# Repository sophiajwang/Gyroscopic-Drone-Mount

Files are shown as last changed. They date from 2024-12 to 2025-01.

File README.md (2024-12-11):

# Gyroscopic Test Rig
#### Sophia Wang and Tshering Dorji

<p align="center">
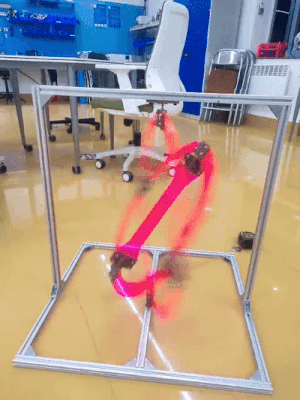
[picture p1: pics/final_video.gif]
animated
  
  <br  /> 3-axis (yaw/pitch/roll) for tuning flight controller pre-launch.
</p>

## Assembly
<p align="center">
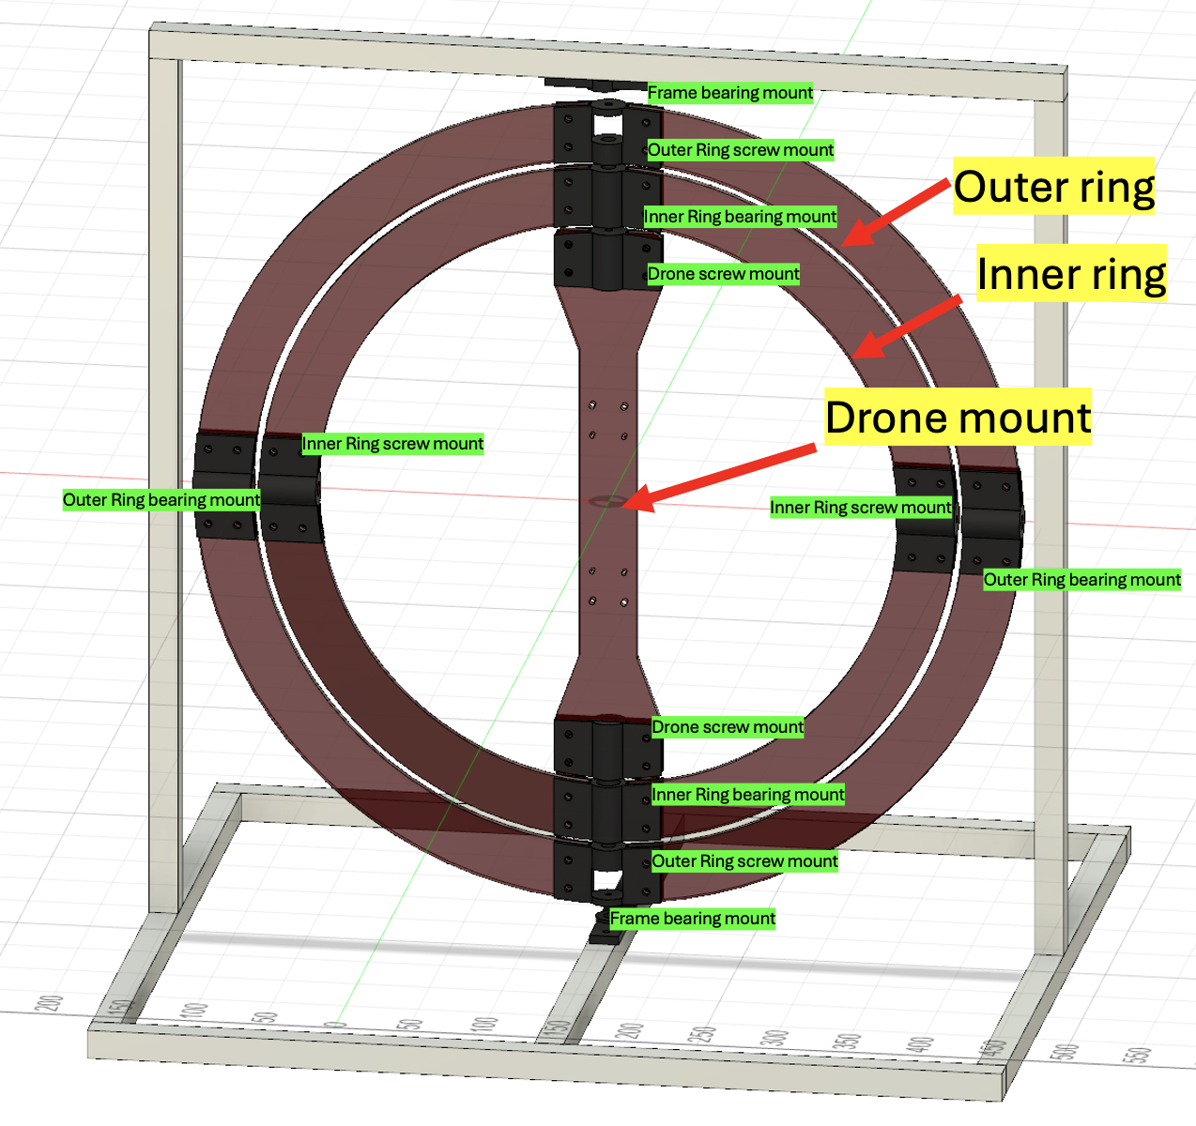
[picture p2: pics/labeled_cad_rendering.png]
  
  <br  /> Assembly Diagram
</p>

## Parts 
### Tools
| Name | Purpose |
| --- | --- |
| Circular saw machine | aluminum extrusions|
| Sanding machine/sandpaper| aluminum extrusions |
| M4 and M5 allen keys | assembly|
| Wrench or needle nose plier | assembly|

### Frame
| Section | Part | Details | Quantity |
| --- | --- | --- | --- |
| Base | Aluminum Extrusion [^1] | 52.5 cm | 3 |
| Base | Aluminum Extrusion | 63 cm | 2 |
| Base | 2020 Corner Bracket | 30 mm x 30 mm | 8 |
| Base | M5x10, knurled cylinder head| | 16 |
| Base | M5 T-nut| | 16 |
| Column | Aluminum Extrusion | 60.5 cm| 2 |
| Column | 2020 Corner Bracket | 30 mm x 30 mm | 4 |
| Column | M5x10, knurled cylinder head| | 8 |
| Column | M5 T-nut| | 8 |
| Top beam | Aluminum Extrusion | 63 cm | 1 |
| Top beam | 2020 Corner Bracket | 30 mm x 30 mm | 2 |
| Top beam | M5x10, knurled cylinder head| | 4 |
| Top beam | M5 T-nut| | 4 |

[^1]: aluminum extrusions are 20 mm x 20 mm, T-Slot 80/20

### Rig
| Section | Part | Details | Quantity |
| --- | --- | --- | --- |
| Mount | Drone Mount | Laser Cut [^2] | 1 |
| Mount | Drone screw mount | 3D print [^3] | 1 |
| Mount | M5x15, knurled cylinder head |  | 8 |
| Mount | M5 nut [^4] |  | 8 |
| Inner Ring | Inner Ring | Laser Cut | 4 |
| Inner Ring | Inner ring screw mount | 3D print | 2 |
| Inner Ring | Inner ring bearing mount | 3D print | 2 |
| Inner Ring | M5x15, knurled cylinder head | ring interconnects | 16 |
| Inner Ring | M5 nut | ring interconnects | 16 |
| Inner Ring | M5x25, knurled cylinder head | bearing shaft [^5] | 2 |
| Inner Ring | M5 nut | bearing shaft | 4 |
| Inner Ring | Bearing (5x16x5mm)	 | | 2 |
| Outer Ring | Outer Ring | Laser Cut | 4 |
| Outer Ring | Outer ring screw mount | 3D print | 2 |
| Outer Ring | Outer ring bearing mount | 3D print | 2 |
| Outer Ring | M5x15, knurled cylinder head | ring interconnects | 16 |
| Outer Ring | M5 nut | ring interconnects | 16 |
| Outer Ring | M5x25, knurled cylinder head | bearing shaft | 2 |
| Outer Ring | M5 nut | bearing shaft | 4 |
| Outer Ring | Bearing (5x13x4mm) | | 2 |
| Frame | Frame Bearing Mount [^6] | 3D print | 2 |
| Frame | M4x30, button cap screw | bearing shaft | 2 |
| Frame | M4 nut | bearing shaft | 6 |

[^2]: 5.5 mm acrylic
[^3]: 30% infil
[^4]: If nuts are difficult to find, you can thread a self-tightening nut with significant elbow grease.
[^5]: We're working around the supply here. Better practice would be to use a fitted 5 mm shaft. Here, we're placing a loosely fitting 5 mm bolt through the shaft of the bearing, and securing with one nut at either end.
[^6]: Again, working around supply. Best case would have been to find some M5x30 bolts, but we were only able to find M4 ones of sufficient length. Here, we're securing the bearing against the head of the bolt and the exacting pressure of the aluminum columns (better to add another nut to relieve precision of extrusions), then securing the screw mount with two nuts.

## Our Process

<p align="middle">
  <br  /> 
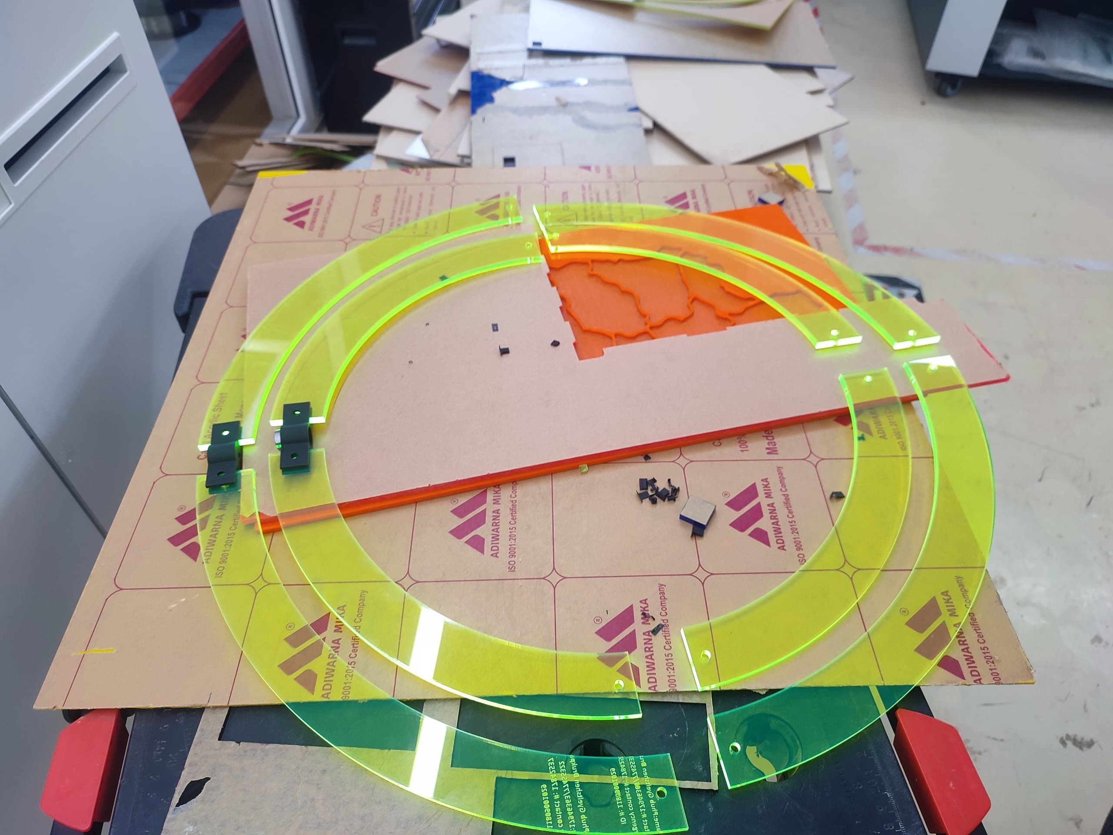
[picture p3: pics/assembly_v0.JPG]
  
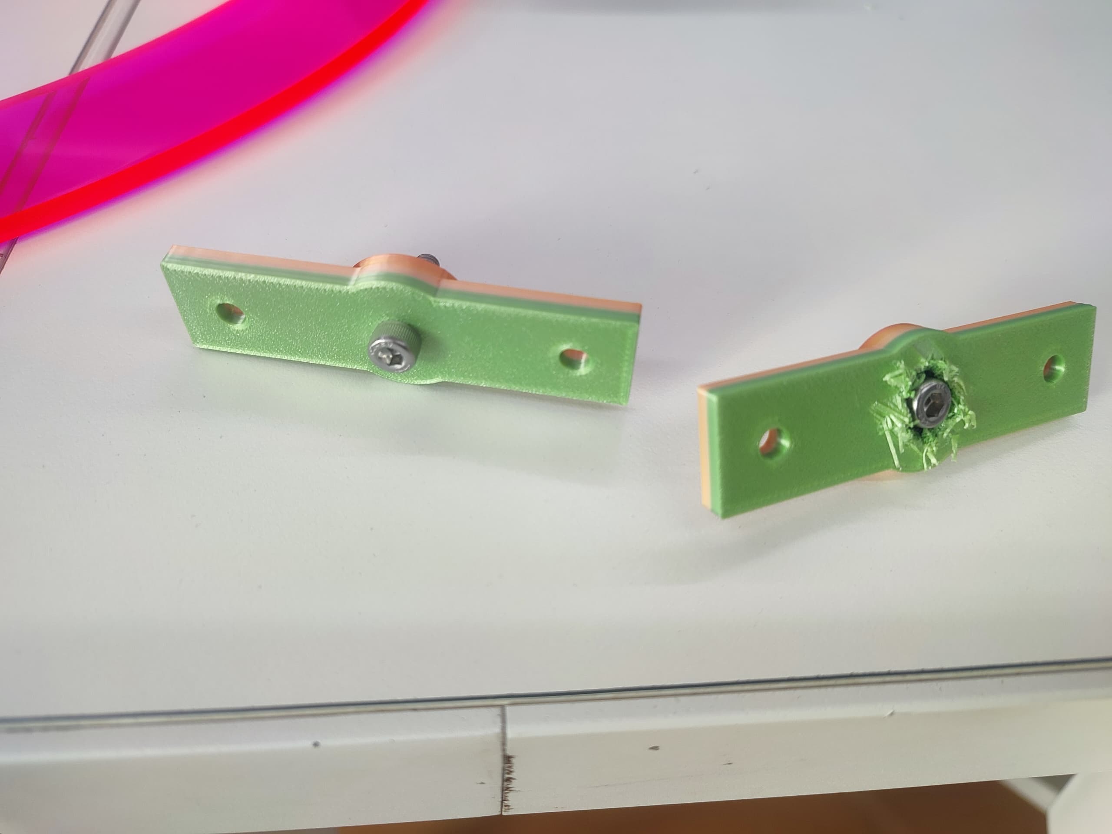
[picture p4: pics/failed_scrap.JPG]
   
  <br  /> attempt 1
</p>

There was lots of trial and error. Our first attempt at nesting the rings was a miscalculation of the degrees of freedom from only one fastener on each side of the screw/bearing mount. These prints don't do well with threading. The shredded PLA you see below is the result of no-tolerance prints, which we quickly adjusted to + 0.15 mm to adjust for post plastic shrinkage. 

<p align="middle">
  <br  /> 
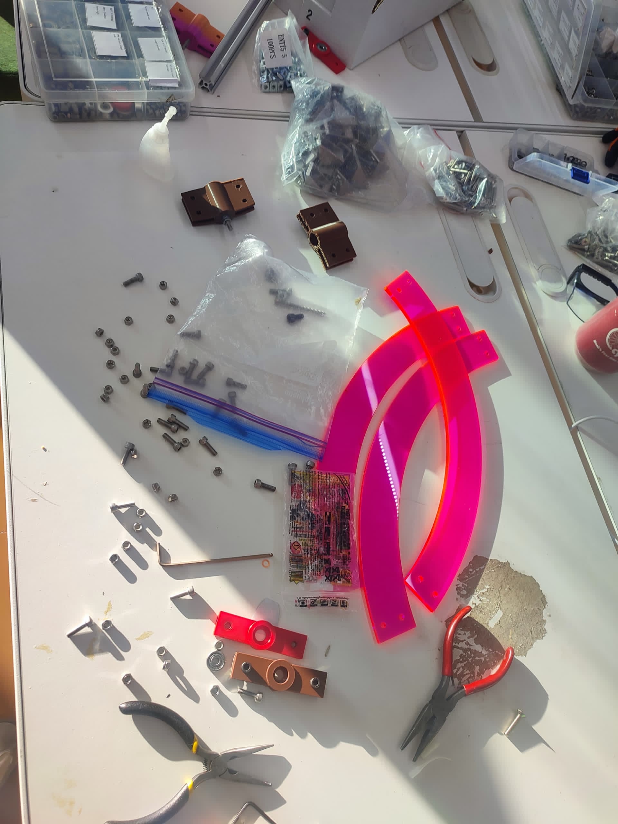
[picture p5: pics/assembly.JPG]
  
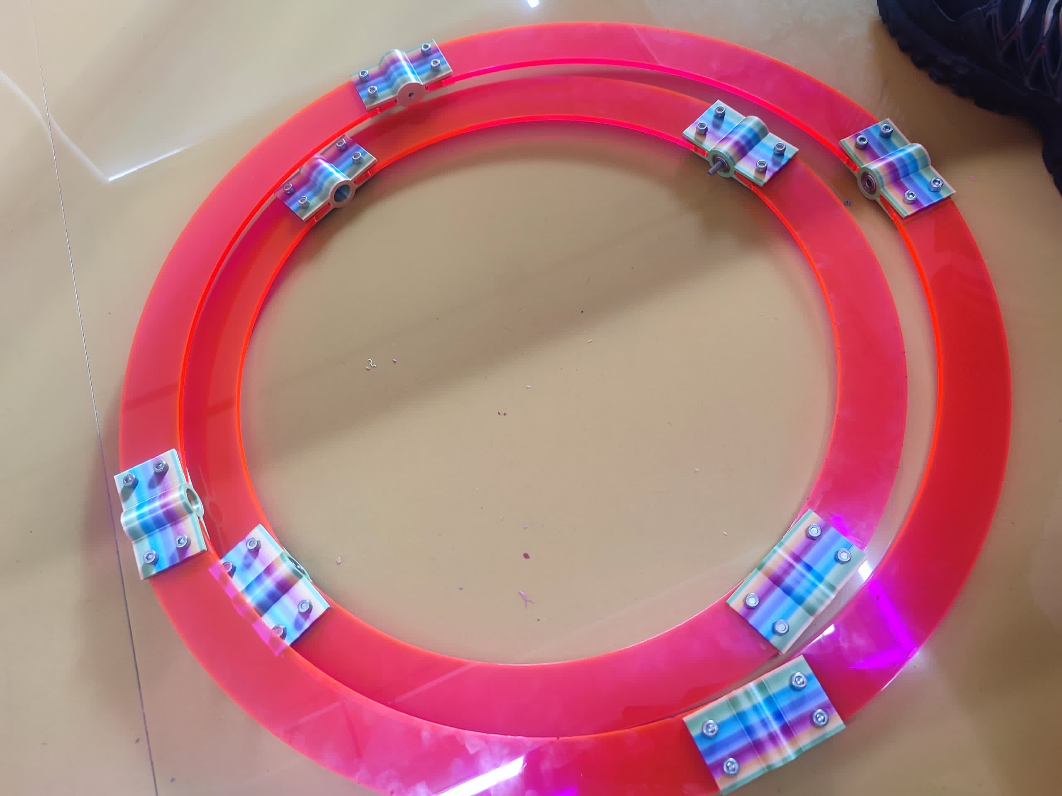
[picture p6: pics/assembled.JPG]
   
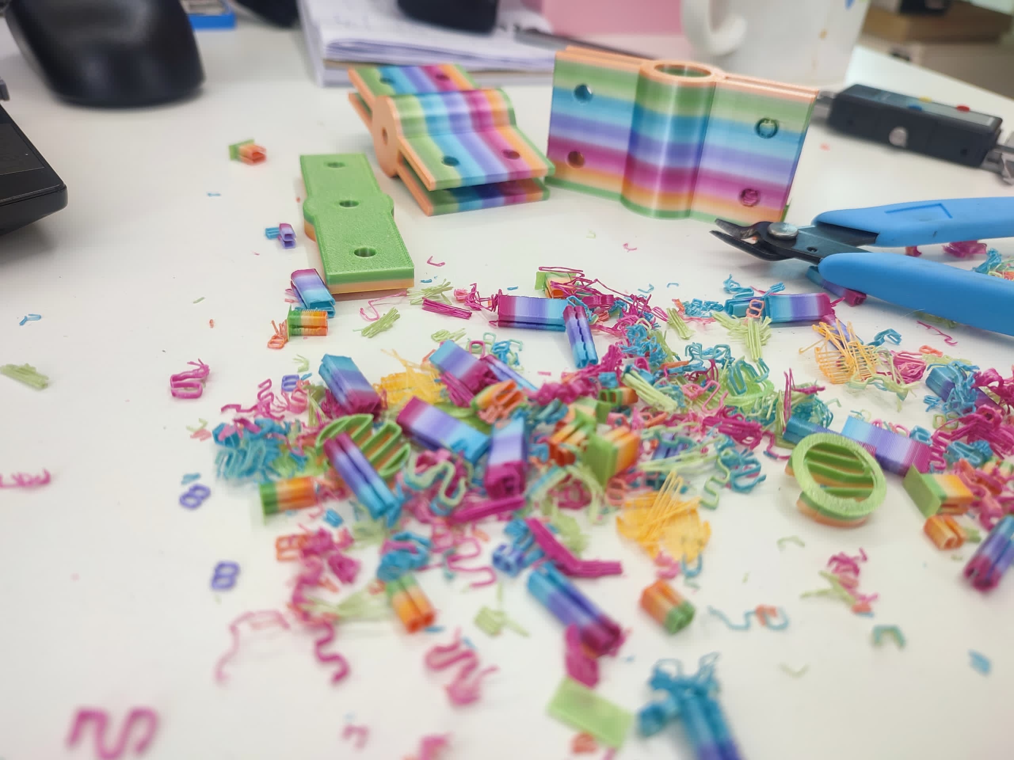
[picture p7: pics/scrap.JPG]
   
  <br  /> attempt 2
</p>

On attempt 2, the realization set in that the M5 screw was too loose as a shaft for the bearing, and without a tight fitting shaft in supply, we opted for a handy nut to secure the bearing's rotational axis. You can see the shredded PLA as we tested this theory out on our existing bearing mounts and realized we needed to redesign to compensate for the extra nut. 

<p align="middle">
  <br  /> 
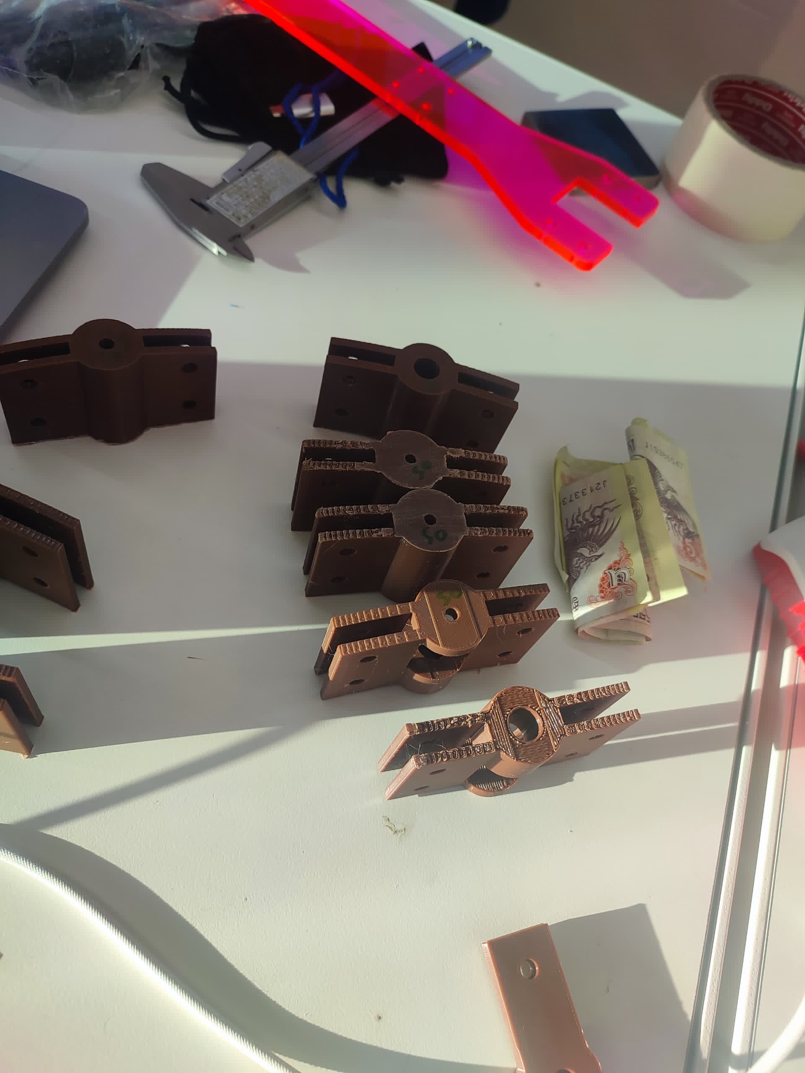
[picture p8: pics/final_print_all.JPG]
  
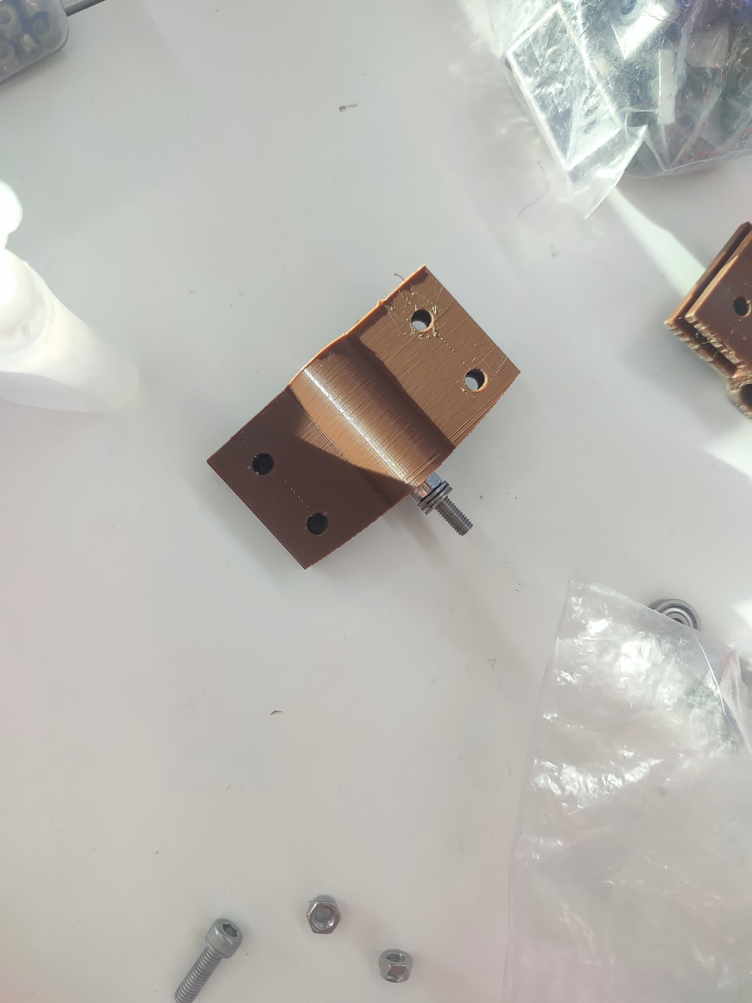
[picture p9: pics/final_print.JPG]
   
  <br  /> attempt 3
</p>

Finally, we could begin cutting the extrusions for the frame and assemble!

<p align="middle">
  <br  /> 
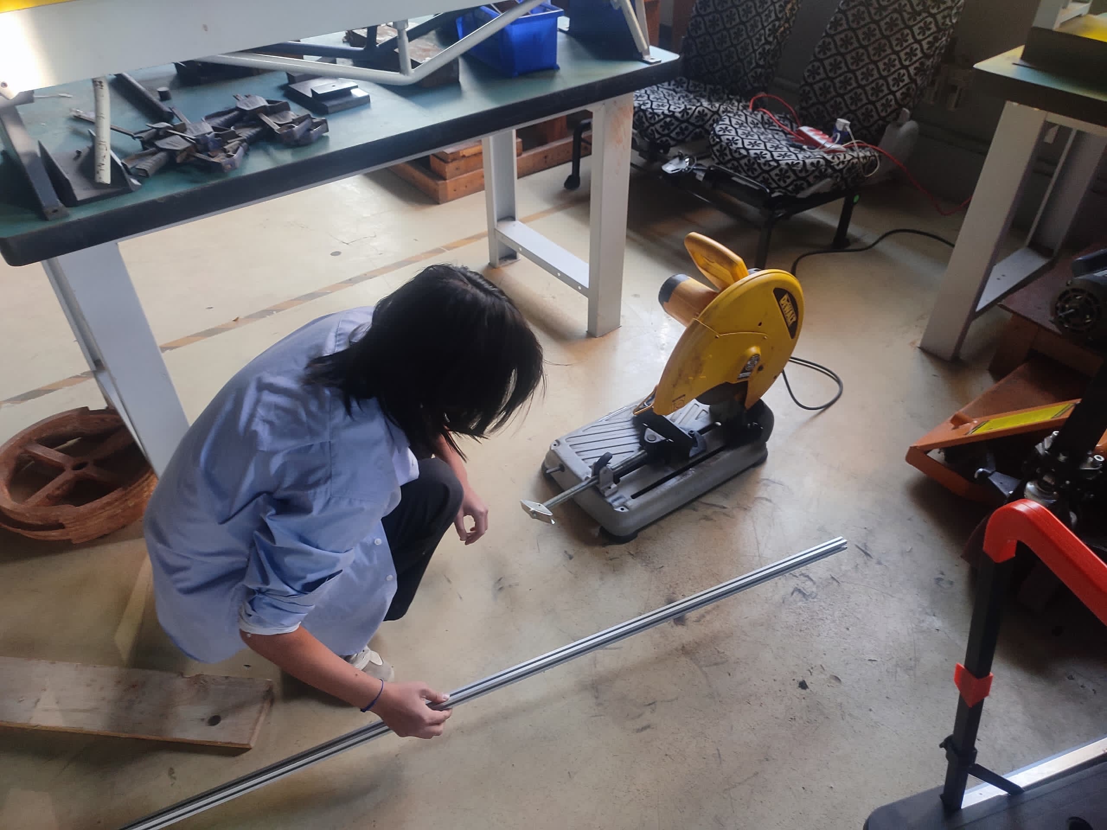
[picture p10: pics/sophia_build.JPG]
  
   
  <br  /> circular saw
</p>

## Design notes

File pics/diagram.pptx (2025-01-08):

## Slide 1

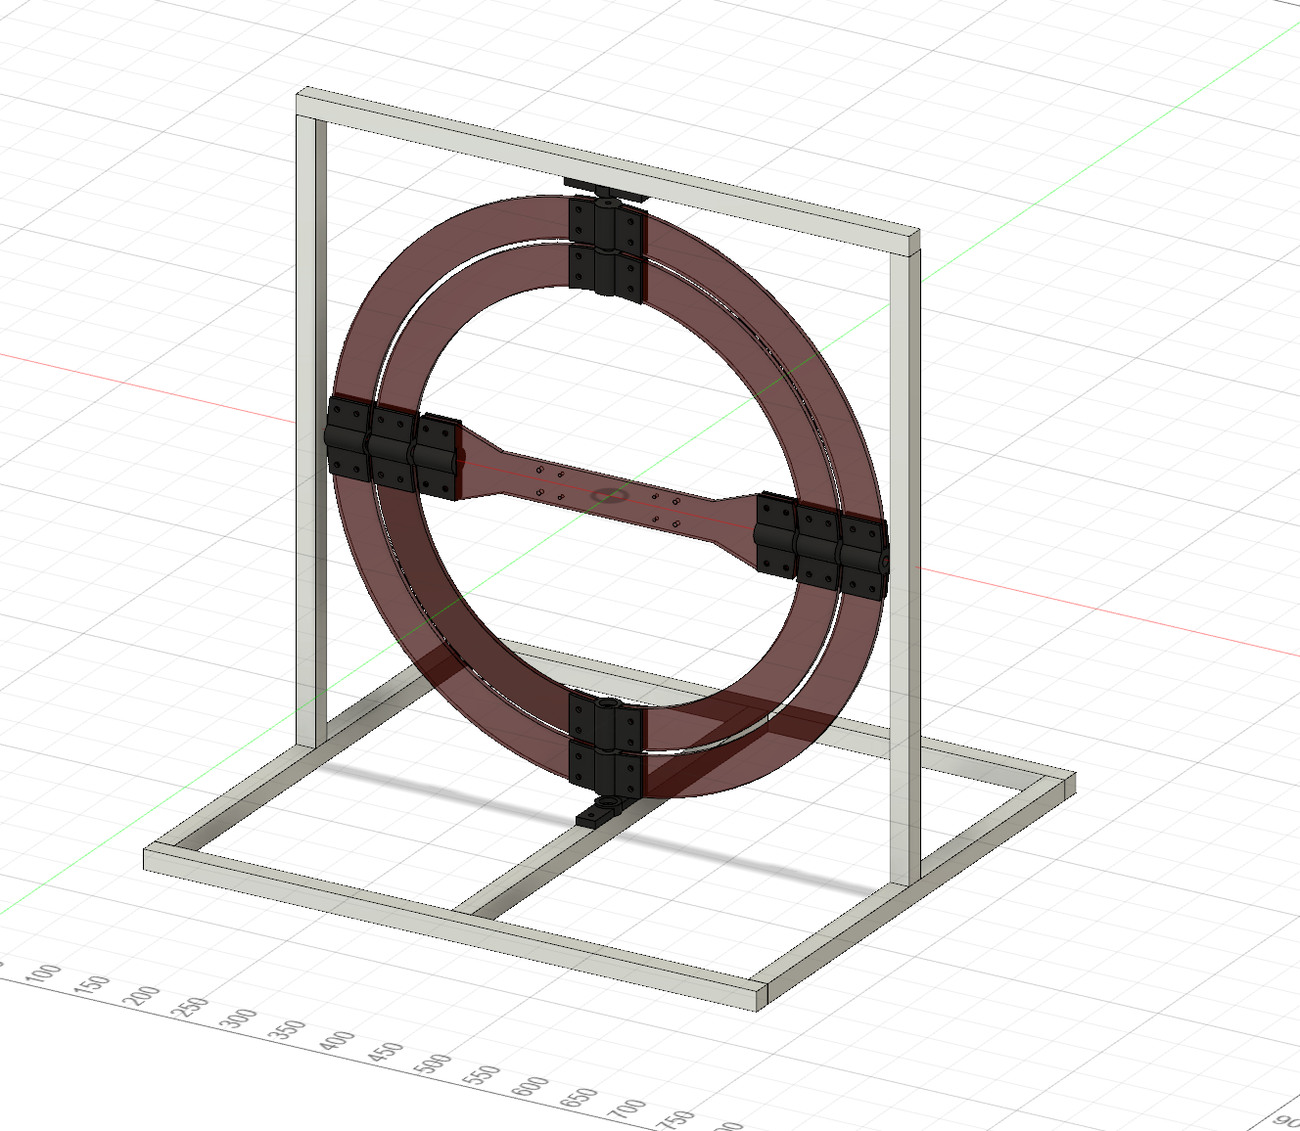
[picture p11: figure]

Frame bearing mount

Outer Ring screw mount

Outer ring

Inner Ring screw mount

Inner ring

Outer Ring bearing mount

Inner Ring bearing mount

Drone mount

Drone screw mount

Drone screw mount

Inner Ring bearing mount

Outer Ring bearing mount

Inner Ring screw mount

Frame bearing mount

Outer Ring screw mount

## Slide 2

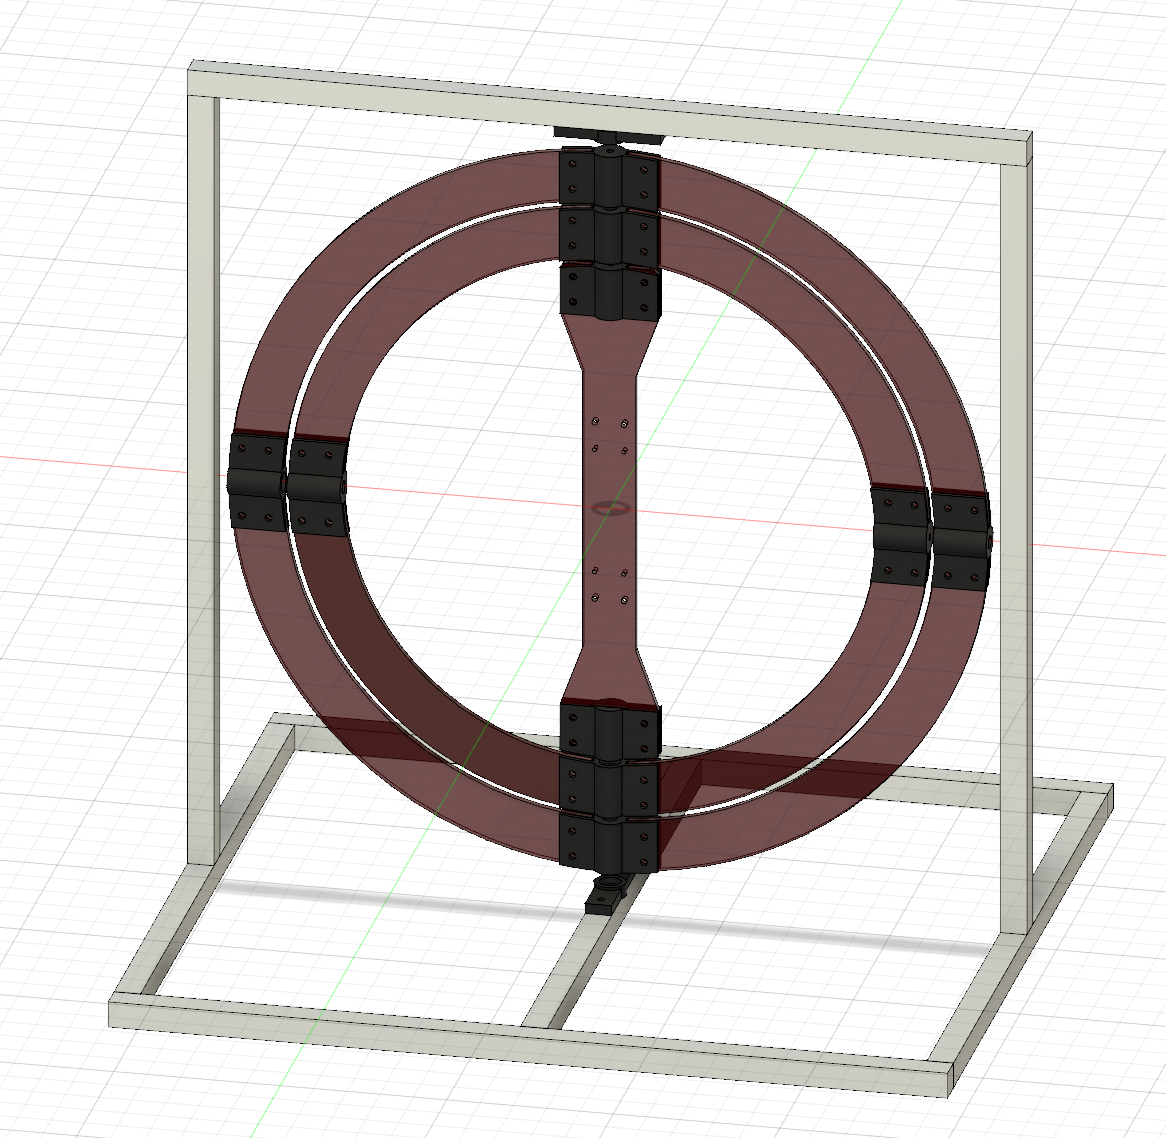
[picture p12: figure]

Frame bearing mount

Outer Ring screw mount

Inner Ring bearing mount

Outer ring

Inner ring

Drone screw mount

Inner Ring screw mount

Drone mount

Inner Ring screw mount

Outer Ring bearing mount

Outer Ring bearing mount

Drone screw mount

Inner Ring bearing mount

Outer Ring screw mount

Frame bearing mount

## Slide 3

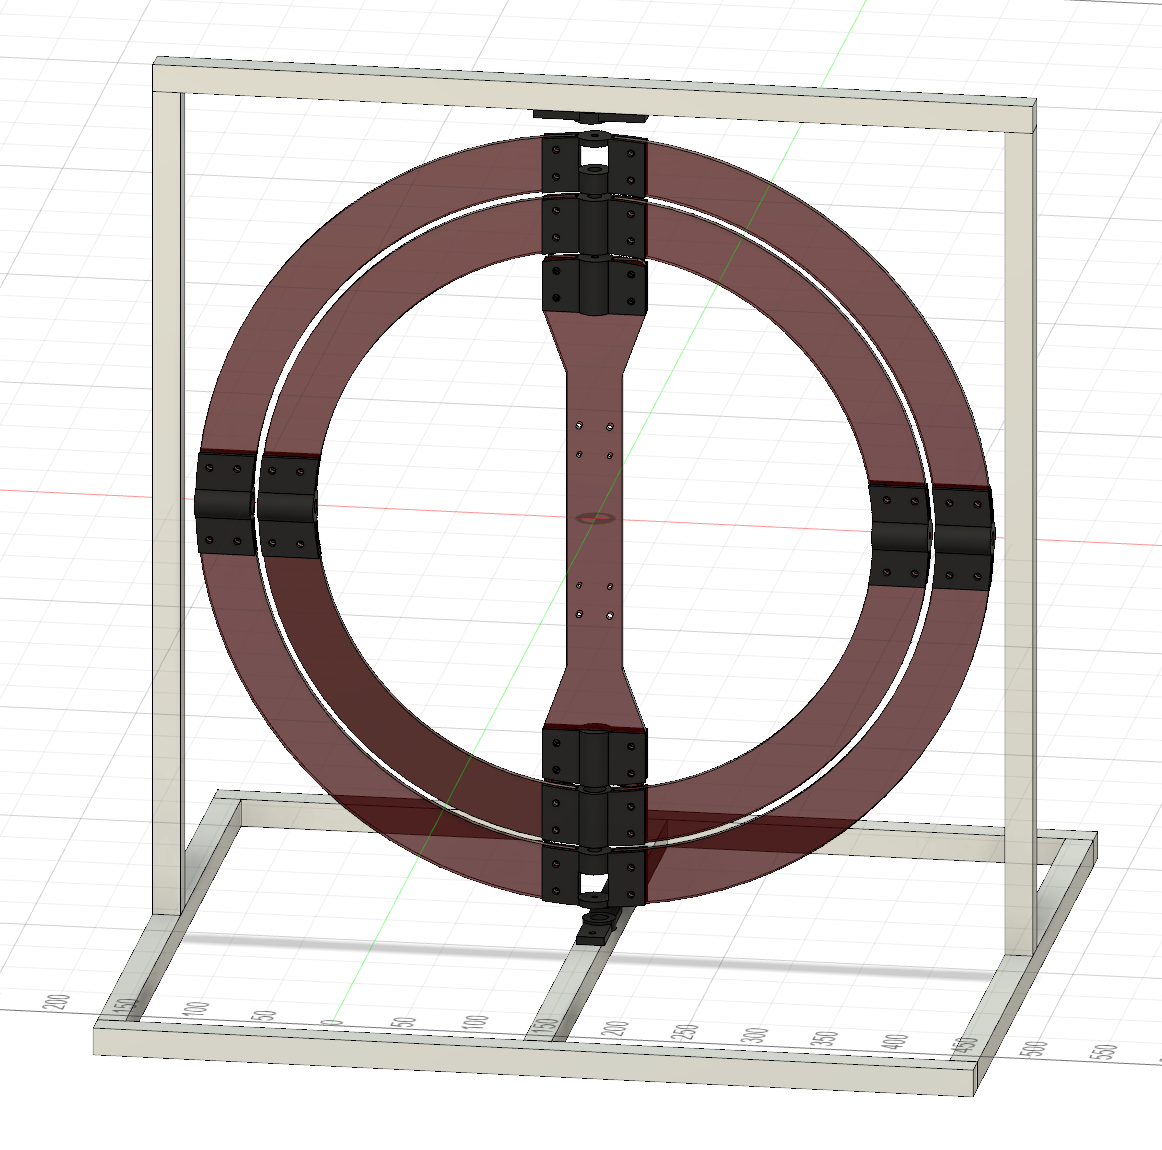
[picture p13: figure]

Frame bearing mount

Outer Ring screw mount

Inner Ring bearing mount

Outer ring

Inner ring

Drone screw mount

Inner Ring screw mount

Drone mount

Inner Ring screw mount

Outer Ring bearing mount

Outer Ring bearing mount

Drone screw mount

Inner Ring bearing mount

Outer Ring screw mount

Frame bearing mount

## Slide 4

Outer ring

Inner ring

Drone mount

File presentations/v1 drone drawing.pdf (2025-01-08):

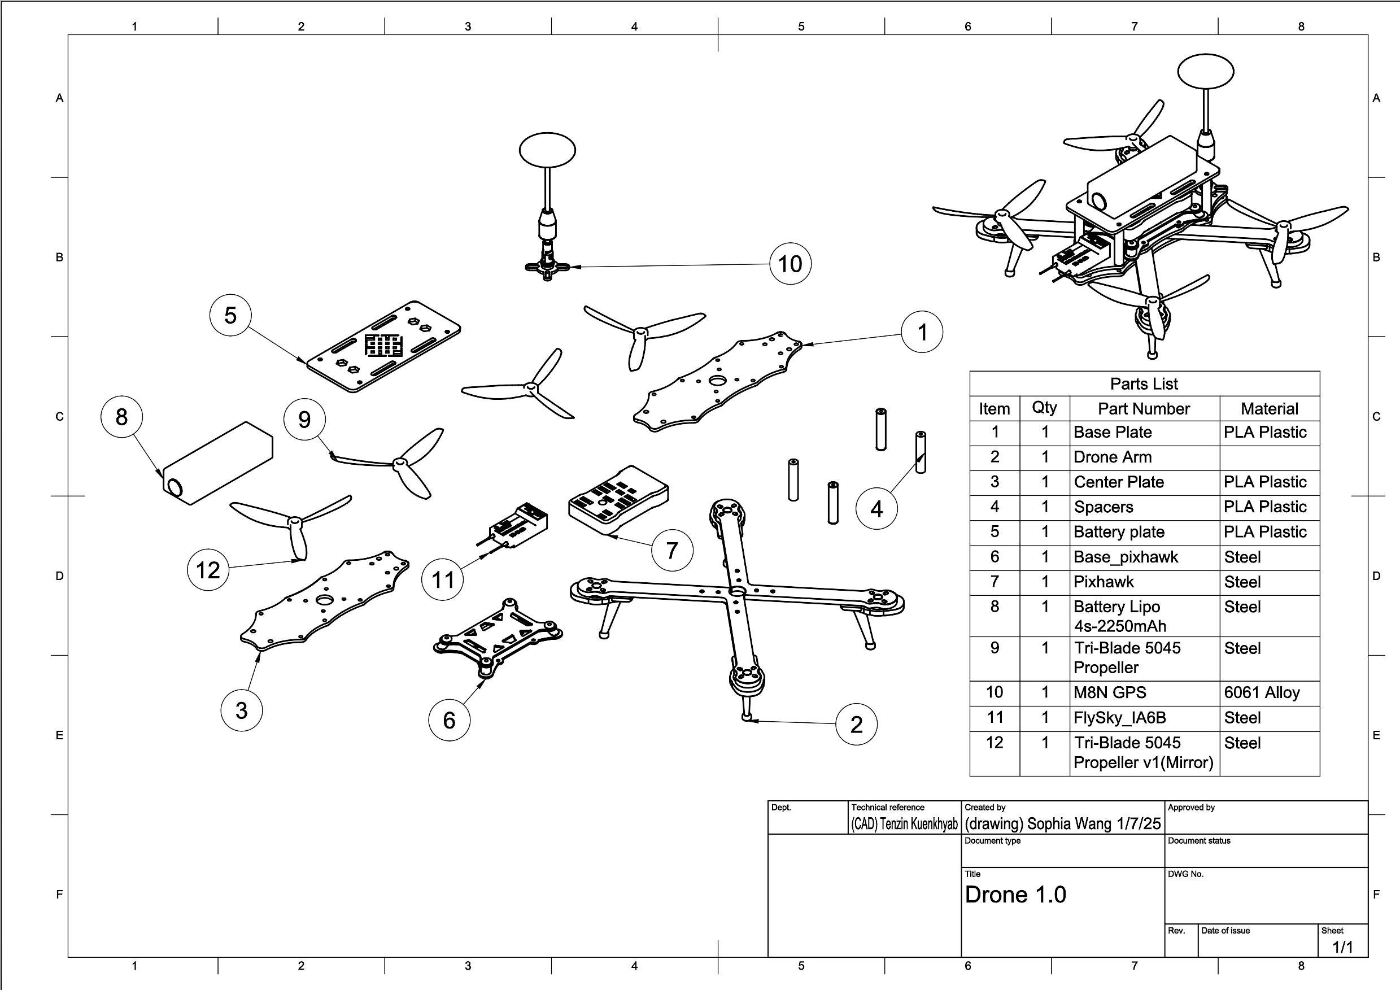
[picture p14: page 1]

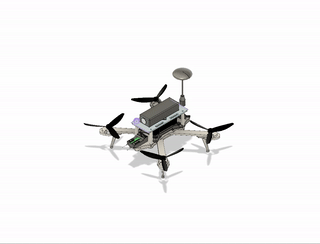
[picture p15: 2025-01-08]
presentations/drone_explode_view.gif

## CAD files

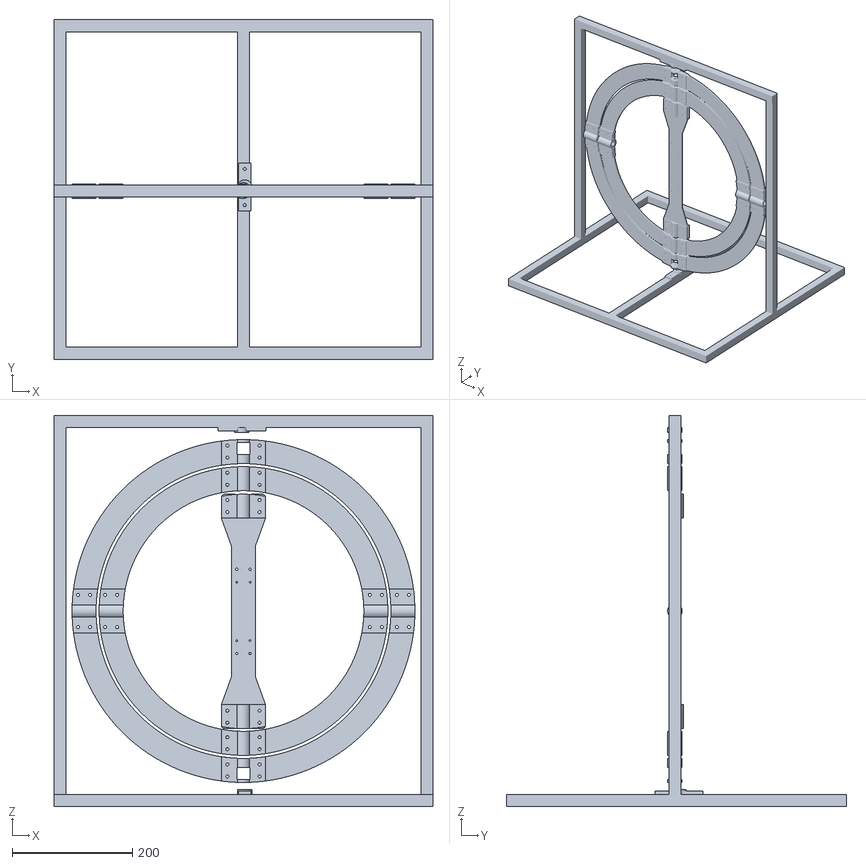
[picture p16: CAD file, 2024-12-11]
cad/Quadcopter Testbed Assembly.stl
630.2 x 564.5 x 650.5

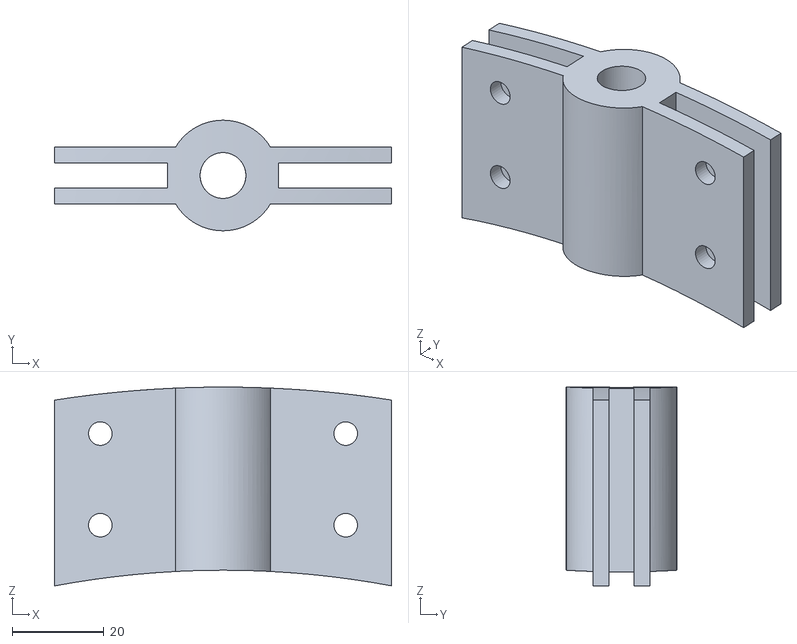
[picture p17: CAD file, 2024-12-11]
cad/inner ring bearing mount.stl
73.6 x 24.1 x 43.4

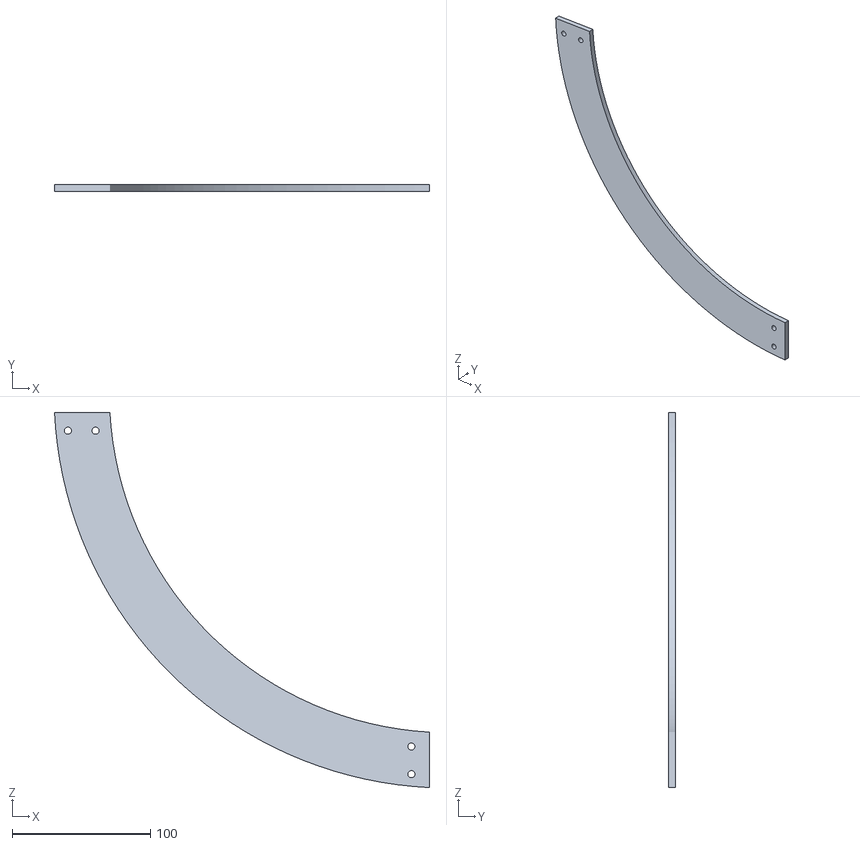
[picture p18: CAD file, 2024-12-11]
cad/outer ring.stl
271.0 x 5.00 x 271.1

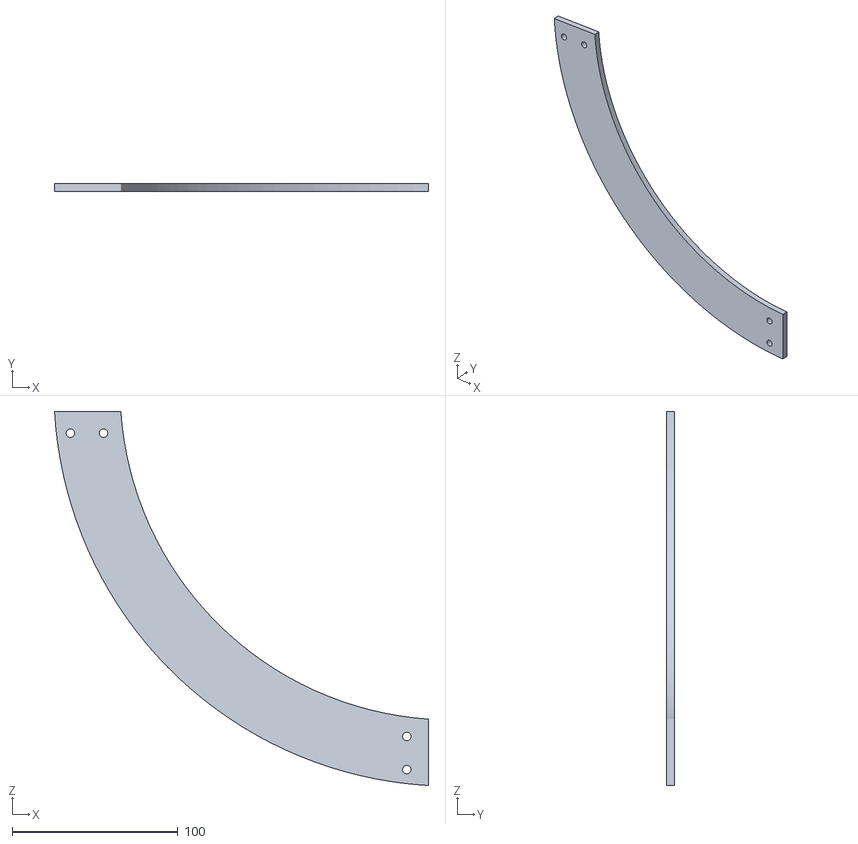
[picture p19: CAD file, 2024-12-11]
cad/inner ring.stl
225.9 x 5.00 x 225.9

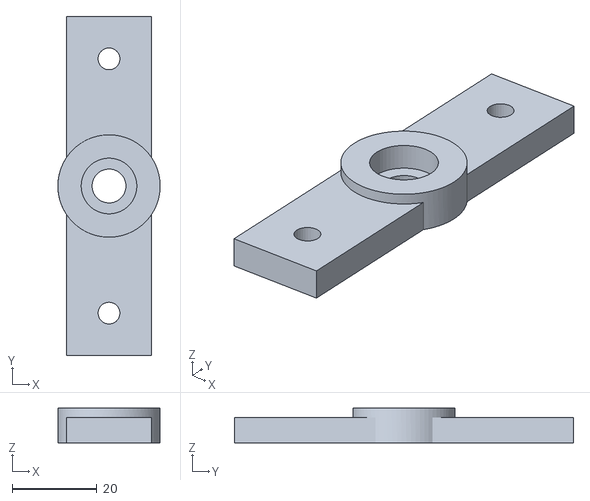
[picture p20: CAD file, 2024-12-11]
cad/frame bearing mount.stl
24.1 x 80.0 x 8.15

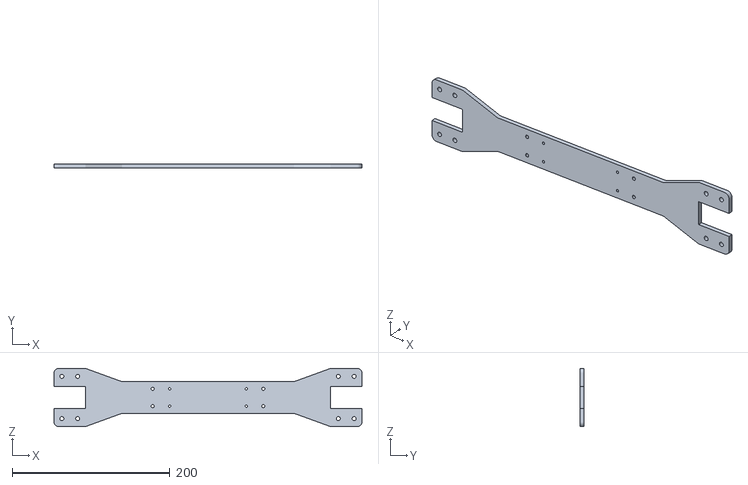
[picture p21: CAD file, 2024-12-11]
cad/drone mount.stl
390.0 x 5.00 x 73.6

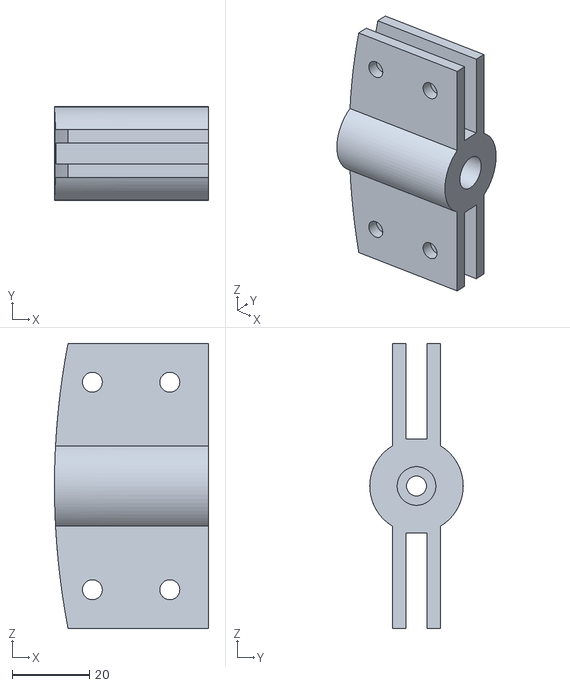
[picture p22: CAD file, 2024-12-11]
cad/drone screw mount.stl
39.8 x 24.2 x 73.6

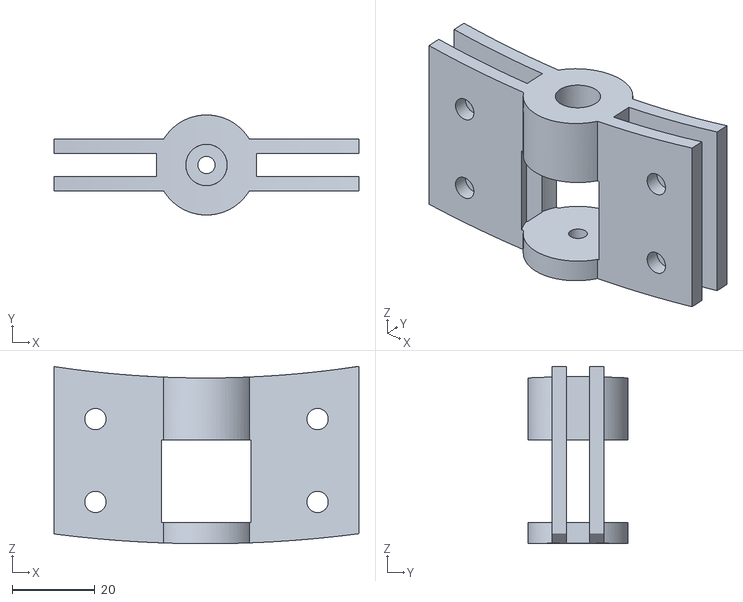
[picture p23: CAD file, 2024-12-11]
cad/outer ring screw mount.stl
73.6 x 24.2 x 42.8

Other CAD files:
cad/outer ring bearing mount.stl
cad/inner ring screw mount.stl
cad/Quadcopter Testbed Assembly.f3d

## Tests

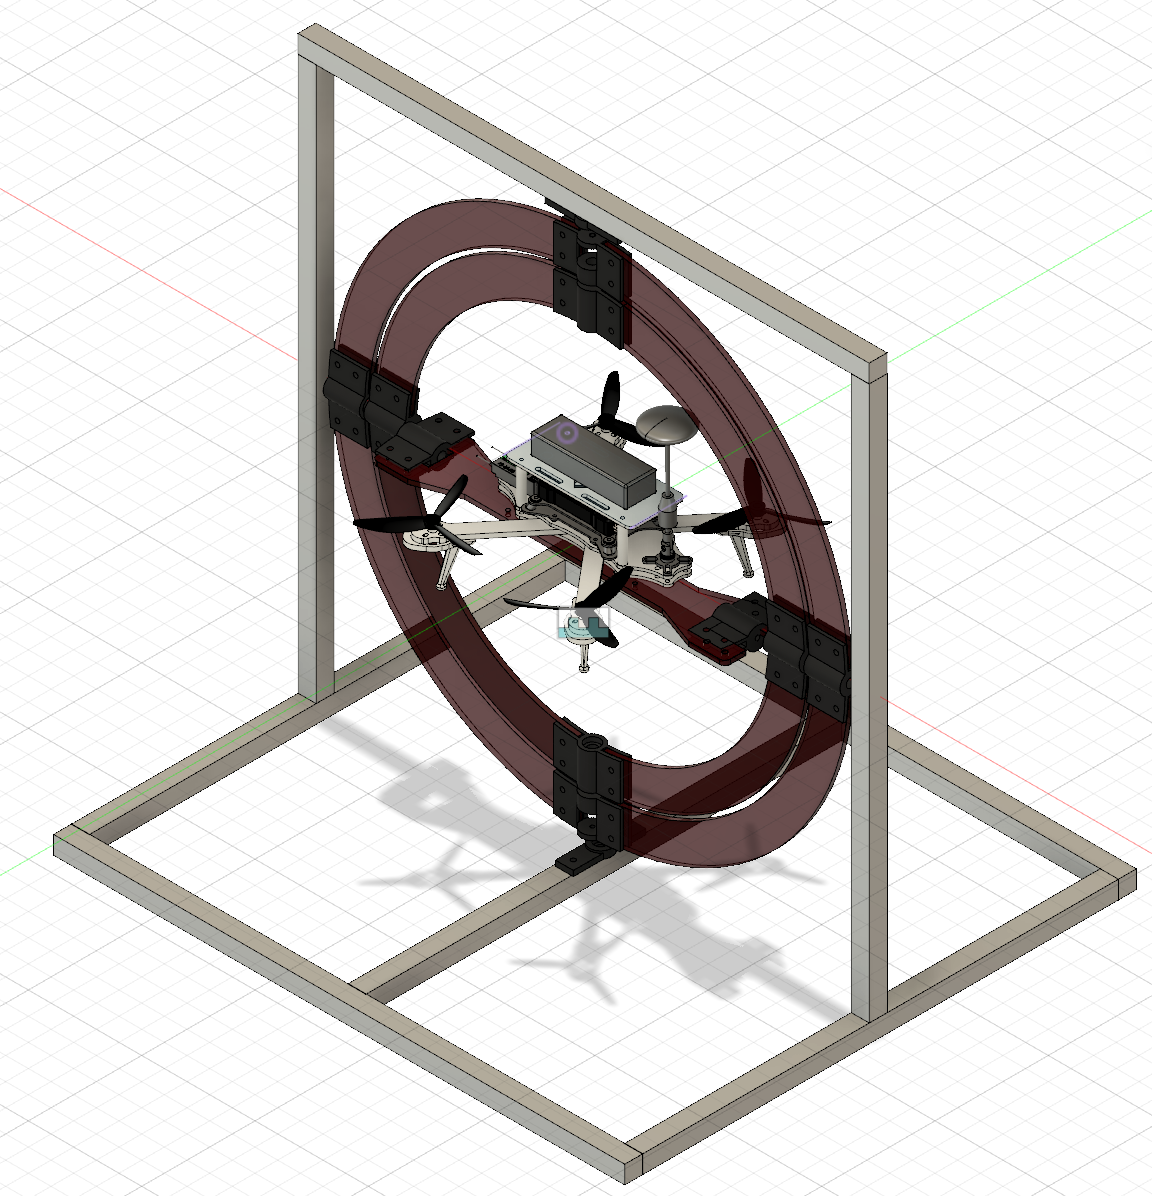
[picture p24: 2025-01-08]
presentations/cad_drone_testrig.png

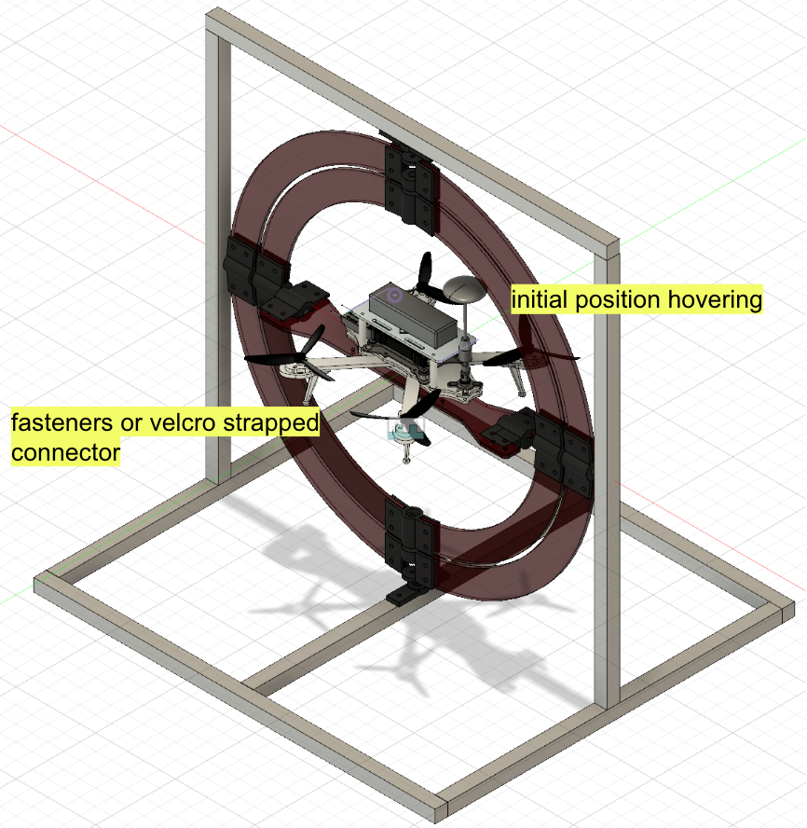
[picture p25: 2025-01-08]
presentations/labeled_cad_drone_testrig.png

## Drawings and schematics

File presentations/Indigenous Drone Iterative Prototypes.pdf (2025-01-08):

# v3 Test Rig

# v3 Controller

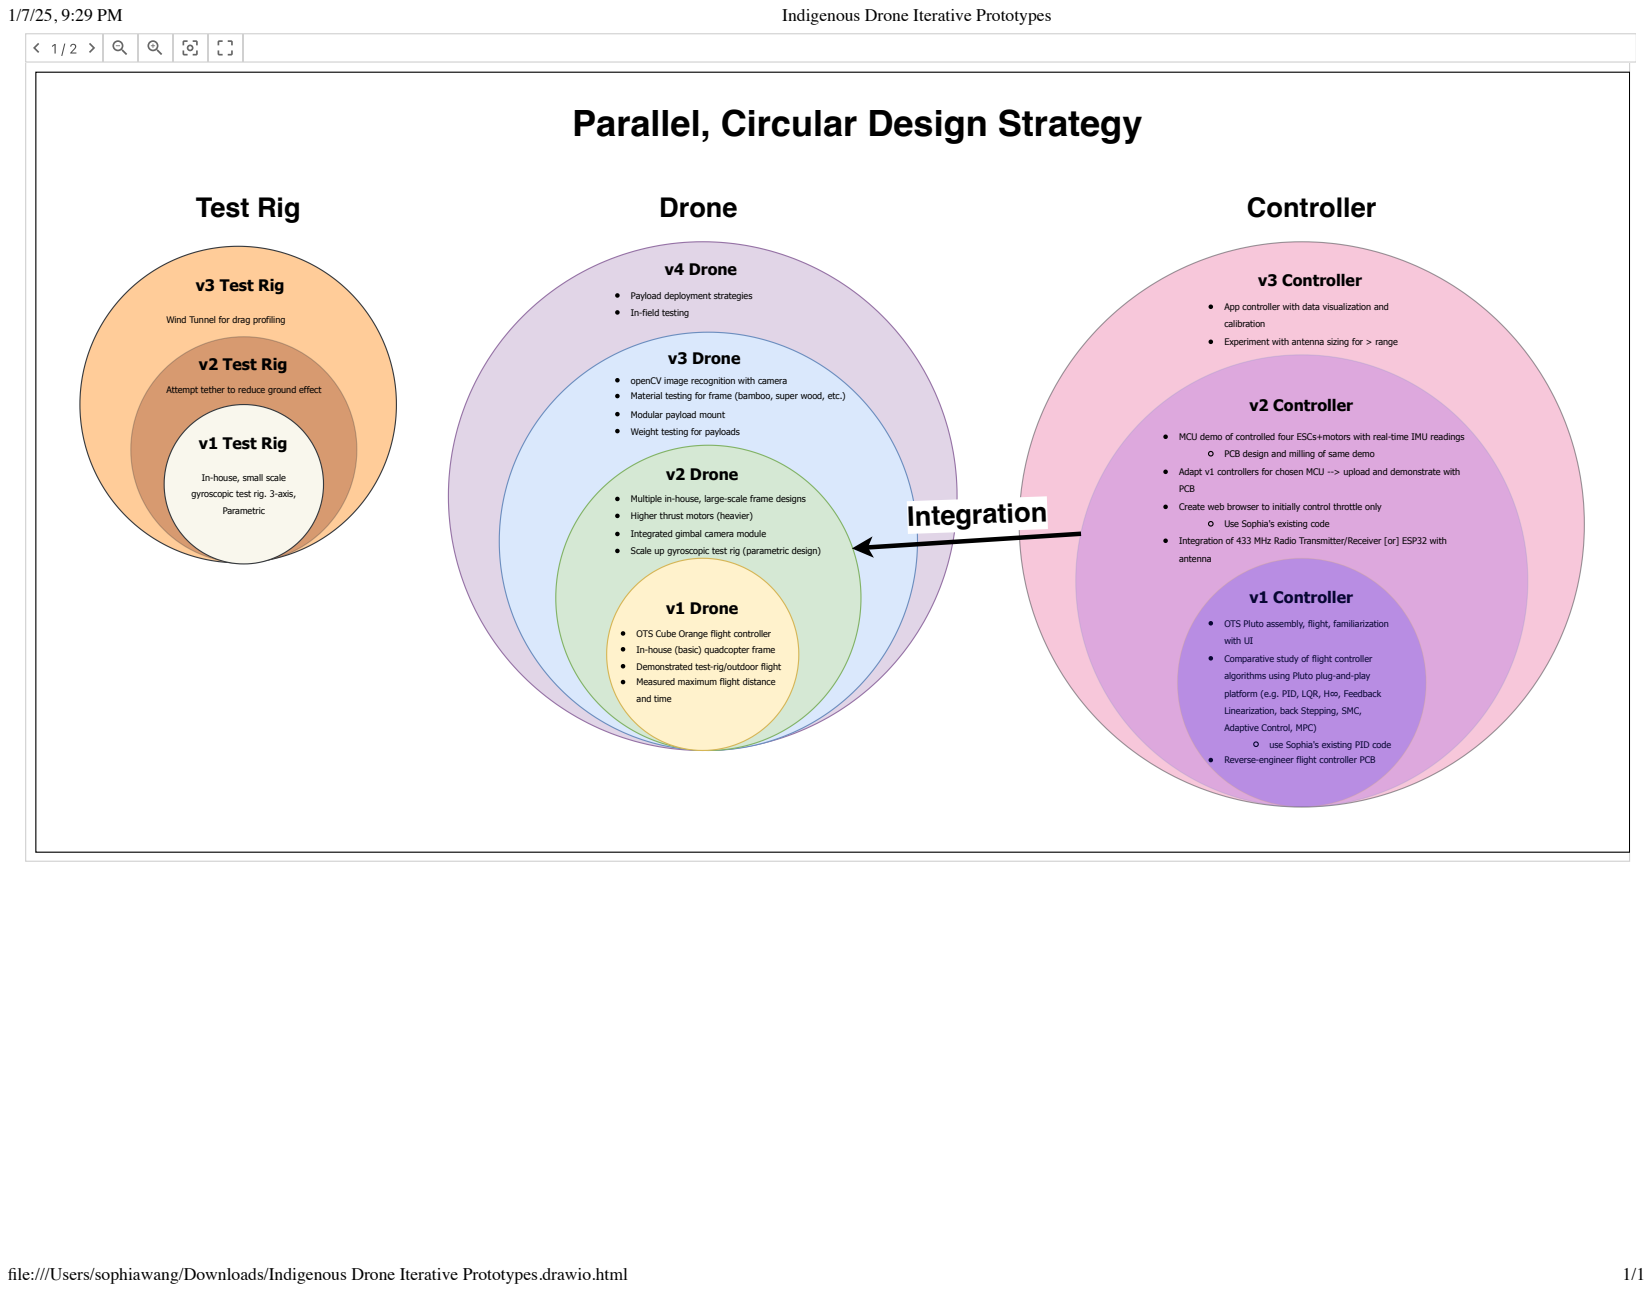
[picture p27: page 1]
v1 Controller; v2 Controller; v1 Test Rig; v2 Test Rig; Drone; Controller; v1 Drone; v3 Drone; v2 Drone; v4 Drone; Integration; Test Rig; Indigenous Drone Iterative Prototypes; file:///Users/sophiawang/Downloads/Indigenous Drone Iterative Prototypes.drawio.html

Parallel, Circular Design Strategy

Payload deployment strategies
In-field testing

Wind Tunnel for drag profiling

App controller with data visualization and
calibration
Experiment with antenna sizing for > range

Attempt tether to reduce ground effect

openCV image recognition with camera
Material testing for frame (bamboo, super wood, etc.)
Modular payload mount
Weight testing for payloads

MCU demo of controlled four ESCs+motors with real-time IMU readings

PCB design and milling of same demo

In-house, small scale
gyroscopic test rig. 3-axis,
Parametric

Adapt v1 controllers for chosen MCU --> upload and demonstrate with
PCB
Create web browser to initially control throttle only

Multiple in-house, large-scale frame designs
Higher thrust motors (heavier)
Integrated gimbal camera module
Scale up gyroscopic test rig (parametric design)

Use Sophia's existing code

Integration of 433 MHz Radio Transmitter/Receiver [or] ESP32 with
antenna

OTS Cube Orange flight controller
In-house (basic) quadcopter frame
Demonstrated test-rig/outdoor flight
Measured maximum flight distance
and time

OTS Pluto assembly, flight, familiarization
with UI
Comparative study of flight controller
algorithms using Pluto plug-and-play
platform (e.g. PID, LQR, H∞, Feedback
Linearization, back Stepping, SMC,
Adaptive Control, MPC)

Reverse-engineer flight controller PCB

use Sophia's existing PID code

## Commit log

2024-12-11 updated files
    [drone mount.stl, drone screw mount.stl, frame bearing mount.stl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]
2024-12-11 updated README and assemblies
    [Quadcopter Testbed Assembly.f3d, Quadcopter Testbed Assembly.stl]
